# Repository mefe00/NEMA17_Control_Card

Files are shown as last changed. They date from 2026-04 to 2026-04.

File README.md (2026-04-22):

# STM32G tabanlı NEMA17 sürücü kartı 

> Bu proje, NEMA17 gibi step motorları alanın az olduğu yerlerde hem kompakt boyut sağlamak hemde kablo karmaşını en aza indirmek için tasarlanmıştır.

resim

## 📋 Özellikler

* MCU: STM32G431CBT6
* Çalışma Gerilimi: 24V
* Haberleşme: CAN/CAN-FD: Kartta iki tane CAN konnektörü vardır. Bu sayede aynı karta veya aynı CAN hattı üzerindeki başka bir kartla haberleşmek için bir konnektöre giriş yapıp diğer konnektörden çıkabilirsiniz ve diğer cihaza giriş yapabilirsiniz. Dikkat: Eğer kartı CAN                   hattının son cihazı ise 60 ohmları buna uygun bir şekilde montajlayın !!!!
              I2C: Eğer motorda redüktör varsa ve kartın arkasındaki encoder kullanılmak istenmezse harici ucuz bir encoder (AS5600) girişi redüktör ucundan alınması içindir. Diğer amacı ise yine bir encoder bağlayıp redüktör boşluğu (backlash) tespiti yapılabilmesi içindir.
              USART: Debug veya direkt haberleşme sağlanabilmesi için. 
* Koruma: 26V seviyesini aşarsa sürücü koruması için TVS diyot
* Encoder: AS5147-P ----> Kartın direkt arkasında bulunur ve pahalı ve kaliteli seçilmesinin sebebi ise redüktör eklenen motorlarda milin daha hızlı dönmesinden dolayı açı verisinin kaçmasını engellemek içindir.
           AS5600   ----> Karta harici bir şekilde girilebilir. Kart üzerinde bunun için harici I2C konnektörü vardır.
* NTC: Kart üzerindeki sıcaklığı tespit etmek için kullanılabilir.
* FAN: NTC'den alınan verilere göre veya manuel soğutma için 24V fan desteği vardır.
* Sürücü: TMC2209 seçilmiştir ama TMC2208 veya pinleri uyuşan başka bir sürücüde kullanılabilir. 

## 📂 Depo İçeriği

* `/Hardware`: KiCAD şematik (`.kicad_sch`) ve PCB (`.kicad_pcb`) tasarım dosyaları.
* `/production`: Üretime hazır Gerber ve Drill dosyaları.
* `/software`: Kartın robot kol eksenlerindeki motorları kontrolü için hazırlanmış gömülü kodu.

## Tavsiyeler

* Güç girişine 50V / 1000uF seviyelerinde bir elektrolit kapasitör eklenmesi.
* Sürücülerin bozulması durumları düşünüldüğü için modül olarak yerleştirilmiştir ve modulün altı boş olduğu için burayada 50V / 220uF seviyelerinde elektrolit kapasitör eklenmesi.
* Daha kararlı bir çalışma olabilmesi için sürücü üzerine soğutucu (heatsink) yerleştirin.
* Daha soğuk bir çalışma için soğutu bloğu buck converter üzerinede yerleştirebilirsiniz.

## Diğer Görseller

resim

resim

FAN

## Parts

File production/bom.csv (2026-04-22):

Designator | Footprint | Quantity | Value | LCSC Part # | Description
C1, C2 | 1206 | 2 | 2.2uF | C50254 | Ceramic Capacitor 2.2uF 50V X7R 10%
C10, C12, C15, C19, C20, C21, C26, C27 | 603 | 8 | 100nF | C14663
C13, C16, C9 | 603 | 3 | 10nF | C100042 | Soft-Start (SS/TR) kapasitörü.
C17, C18, C23, C25, C28 | 603 | 5 | 1uF | C15849
C22, C24 | 603 | 2 | 20pF | C1648
C3 | 603 | 1 | 0.1uF | C53084455 | C3 giriş filtresi, C8 ise BOOT kapasitörü
C4 | 603 | 1 | 6800pF | C107097 | Kompanzasyon (COMP) ağı kapasitörü.
C5 | 603 | 1 | 39pF | C107049 | Kompanzasyon (COMP) ağı yüksek frekans kapasitörü (NP0/C0G dielektrik).
C6, C7 | 805 | 2 | 47uF | C6119904 | 5V çıkış hattı filtre kapasitörleri. 5V için 10V voltaj dayanımı yeterlidir.
C8 | 603 | 1 | 10uF | C53084455
D1 | D_SMA | 1 | B260 | C109094 | 60V 2A Schottky Diyot. (MCU ve sensörler için 2A fazlasıyla yeterli)
D2 | D_SOD-323 | 1 | 1N5819WS | C191023
D3 | DIO_PESD2CAN_215 | 1 | PESD2CANFD24 | C5278878
D4 | 603 | 1 | GREEN | C2986048
D5 | 603 | 1 | RED | C183848
D6 | D_SMB | 1 | SMBJ26A-13-F | C135062 | TVS Diode Unidirectional 26V WM 600W
FB1 | 603 | 1 | FerriteBead | C14709
J1 | AMASS_XT30U-F_1x02_P5.0mm_Vertical | 1 | Conn_01x02_Socket
J10, J8, J9 | JST_GH_SM04B-GHS-TB_1x04-1MP_P1.25mm_Horizontal | 3 | Conn_01x04_Socket | C189895
J2, J3 | PinHeader_1x02_P2.54mm_Vertical | 2 | Conn_01x02_Pin
J4 | JST_PH_S4B-PH-K_1x04_P2.00mm_Horizontal | 1 | Conn_01x04_Socket
J5, J6 | JST_GH_SM02B-GHS-TB_1x02-1MP_P1.25mm_Horizontal | 2 | Conn_01x02_Socket | C189893
L1 | L_6.3x6.3_H3 | 1 | 8.2uH | C167222 | 6x6x2.8mm SMD Bobin (Sunlord). Doyuma ulaşma akımı 2.5A, bu sistem için ideal.
Q1 | SOT-23 | 1 | AO3400A | C20917
R1 | 603 | 1 | 162k | C2998114 | EN (Enable) pini voltaj bölücü alt direnci.
R11 | 603 | 1 | 2.2k -1k | C22548
R12, R15, R18, R8, R9 | 603 | 5 | 10k | C98220
R13 | 603 | 1 | 330R | C105881
R16, R17 | 603 | 2 | 60R | C85834
R2 | 603 | 1 | 523k | C5126197 | EN (Enable) pini voltaj bölücü üst direnci.
R3 | 603 | 1 | 84.5k | C855976 | RT/CLK frekans ayar direnci.
R4 | 603 | 1 | 13k | C137796 | Kompanzasyon (COMP) ağı direnci.
R5 | 603 | 1 | 53.6k | C2930115 | Feedback (FB) üst direnci (Hassas 5V çıkış için %1 tolerans).
R6 | 603 | 1 | 10.2k | C22772 | Feedback (FB) alt direnci (Hassas 5V çıkış için %1 tolerans).
R7 | 603 | 1 | 100R | C105588
SW1 | SW_Push_1P1T_NO_CK_KMR2 | 1 | SW_Push | C99271
U1 | LQFP-48_7x7mm_P0.5mm | 1 | STM32G431CBT6 | C529355 | MCU
U2 | SOT-23-5 | 1 | AP2112K-3.3 | C51118 | 3.3V LDO
U3 | TI_SO-PowerPAD-8_ThermalVias | 1 | TPS54360DDA | C465733 | 60V, 3.5A Step-Down Converter
U4 | SOIC-8_3.9x4.9mm_P1.27mm | 1 | MCP2562-E-SN | C53609 | CAN entegresi
U5 | MODULE_TMC2209_SILENTSTEPSTICK | 1 | TMC2209_SILENTSTEPSTICK
U6 | TSSOP-14_AMS | 1 | AS5147P-HTSM | C22426928 | Encoder
Y1 | Crystal_SMD_3225-4Pin_3.2x2.5mm | 1 | Crystal_GND24_Small | C7275084 | Kristal

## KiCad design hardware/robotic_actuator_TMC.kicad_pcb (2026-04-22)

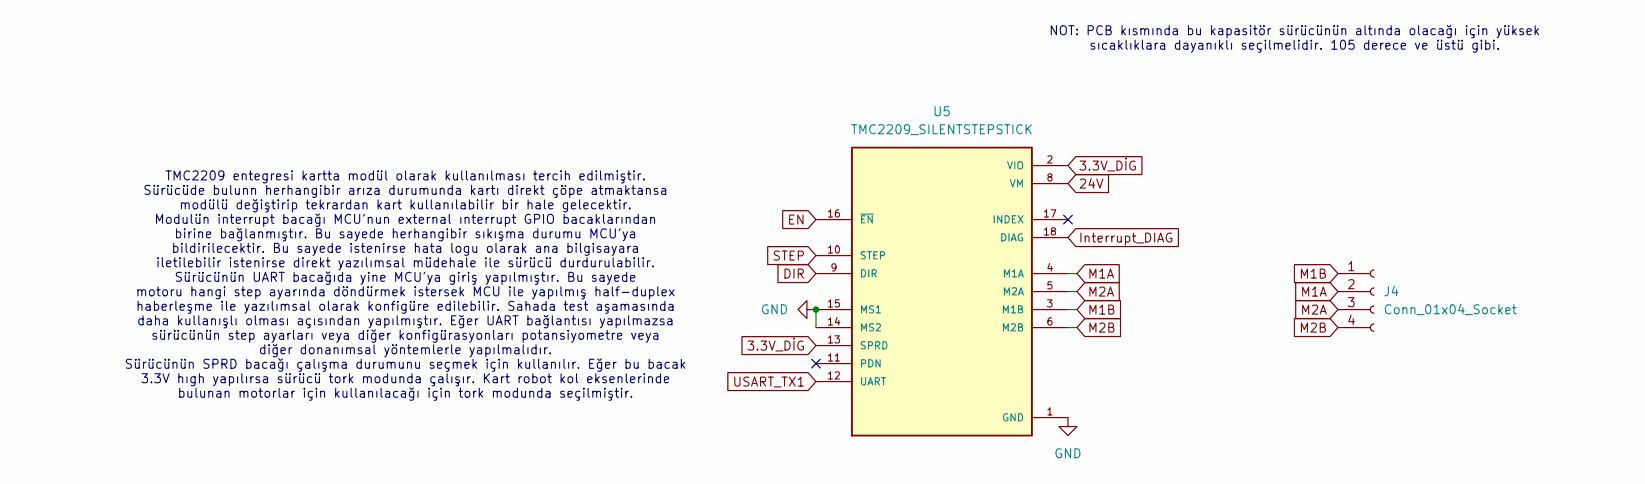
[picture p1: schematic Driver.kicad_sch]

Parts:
J4: Conn_01x04_Socket; JST_PH_S4B-PH-K_1x04_P2.00mm_Horizontal
U5: TMC2209_SILENTSTEPSTICK; MODULE_TMC2209_SILENTSTEPSTICK; PARTREV 1.20

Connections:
3.3V_DİG: U5.2 (VIO), U5.13 (SPRD); also elsewhere on the board
24V: U5.8 (VM); also elsewhere on the board
DIR: U5.9 (DIR); also elsewhere on the board
EN: U5.16 (~EN); also elsewhere on the board
GND: U5.1 (GND), U5.7 (GND), U5.14 (MS2), U5.15 (MS1); also elsewhere on the board
Interrupt_DIAG: U5.18 (DIAG); also elsewhere on the board
M1A: J4.2, U5.4 (M1A)
M1B: J4.1, U5.3 (M1B)
M2A: J4.3, U5.5 (M2A)
M2B: J4.4, U5.6 (M2B)
STEP: U5.10 (STEP); also elsewhere on the board
USART_TX1: U5.12 (UART); also elsewhere on the board

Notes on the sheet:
TMC2209 entegresi kartta modül olarak kullanılması tercih edilmiştir. Sürücüde bulunn herhangibir arıza durumunda kartı direkt çöpe atmaktansa modülü değiştirip tekrardan kart kullanılabilir bir hale gelecektir. Modulün interrupt bacağı MCU'nun external ınterrupt GPIO bacaklarından birine bağlanmış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
NOT: PCB kısmında bu kapasitör sürücünün altında olacağı için yüksek sıcaklıklara dayanıklı seçilmelidir. 105 derece ve üstü gibi.

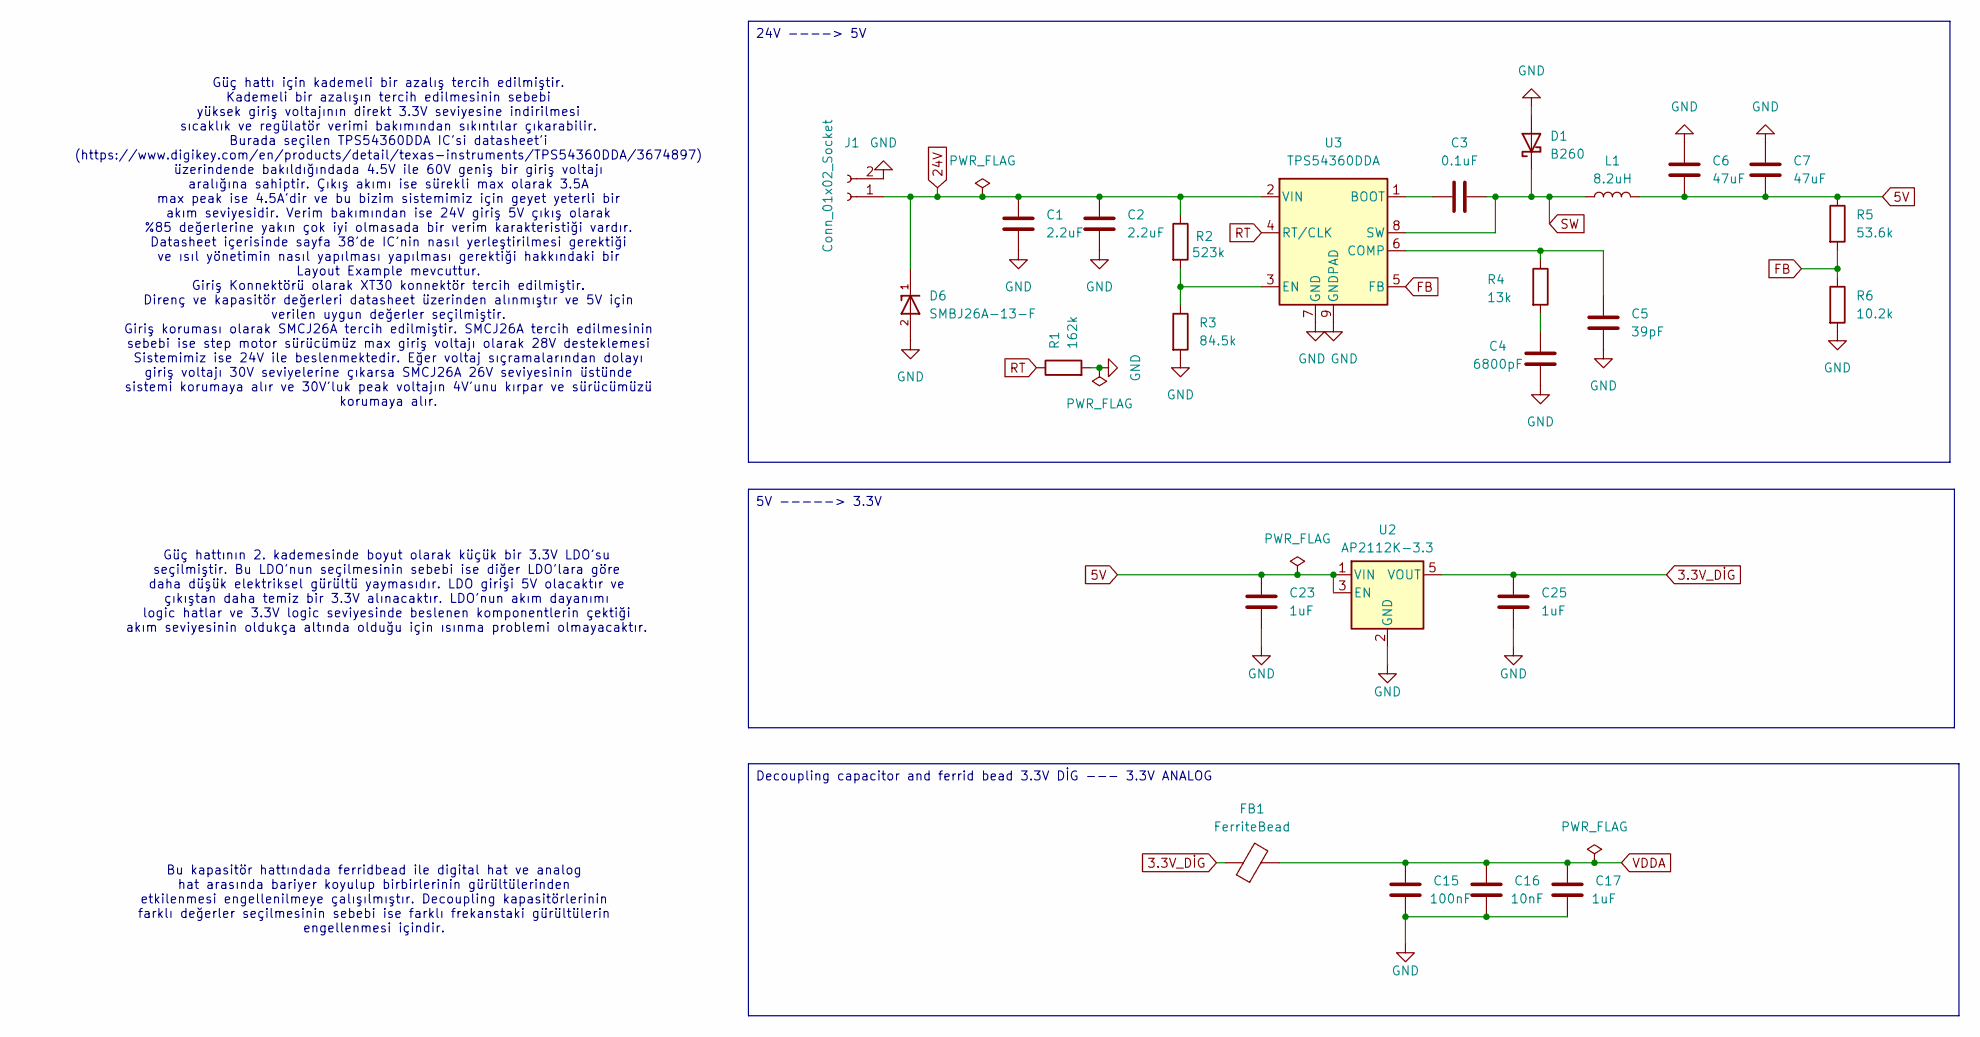
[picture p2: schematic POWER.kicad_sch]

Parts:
C1, C2: 2.2uF; C_1206_3216Metric
C3: 0.1uF; C_0603_1608Metric
C4: 6800pF; C_0603_1608Metric
C5: 39pF; C_0603_1608Metric
C6, C7: 47uF; C_0805_2012Metric
C15: 100nF; C_0603_1608Metric
C16: 10nF; C_0603_1608Metric
C17, C23, C25: 1uF; C_0603_1608Metric
D1: B260; D_SMA
D6: SMBJ26A-13-F; D_SMB; PARTREV 20 - 2
FB1: FerriteBead; L_0603_1608Metric
J1: Conn_01x02_Socket; AMASS_XT30U-F_1x02_P5.0mm_Vertical
L1: 8.2uH; L_6.3x6.3_H3
R1: 162k; R_0603_1608Metric
R2: 523k; R_0603_1608Metric
R3: 84.5k; R_0603_1608Metric
R4: 13k; R_0603_1608Metric
R5: 53.6k; R_0603_1608Metric
R6: 10.2k; R_0603_1608Metric
U2: AP2112K-3.3; SOT-23-5
U3: TPS54360DDA; TI_SO-PowerPAD-8_ThermalVias

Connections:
3.3V_DİG: C25.1, FB1.1, U2.5 (VOUT); also elsewhere on the board
5V: C6.1, C7.1, C23.1, L1.2, R5.1, U2.1 (VIN), U2.3 (EN); also elsewhere on the board
24V: C1.1, C2.1, D6.1, J1.1, R2.1, U3.2 (VIN); also elsewhere on the board
FB: R5.2, R6.1, U3.5 (FB)
GND: C1.2, C2.2, C4.1, C5.1, C6.2, C7.2, C15.2, C16.2, C17.2, C23.2, C25.2, D1.2 (A), D6.2, J1.2, R1.2, R3.2, R6.2, U2.2 (GND), U3.7 (GND), U3.9 (GNDPAD); also elsewhere on the board
unnamed: C4.2, R4.2
unnamed: C3.1, U3.1 (BOOT)
unnamed: C5.2, R4.1, U3.6 (COMP)
unnamed: R2.2, R3.1, U3.3 (EN)
RT: R1.1, U3.4 (RT/CLK)
SW: C3.2, D1.1 (K), L1.1, U3.8 (SW)
VDDA: C15.1, C16.1, C17.1, FB1.2; also elsewhere on the board

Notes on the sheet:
Güç hattının 2. kademesinde boyut olarak küçük bir 3.3V LDO'su seçilmiştir. Bu LDO'nun seçilmesinin sebebi ise diğer LDO'lara göre daha düşük elektriksel gürültü yaymasıdır. LDO girişi 5V olacaktır ve çıkıştan daha temiz bir 3.3V alınacaktır. LDO'nun akım dayanımı logic hatlar ve 3.3V logic seviyes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
Bu kapasitör hattındada ferridbead ile digital hat ve analog hat arasında bariyer koyulup birbirlerinin gürültülerinden etkilenmesi engellenilmeye çalışılmıştır. Decoupling kapasitörlerinin farklı değerler seçilmesinin sebebi ise farklı frekanstaki gürültülerin engellenmesi içindir.
Güç hattı için kademeli bir azalış tercih edilmiştir. Kademeli bir azalışın tercih edilmesinin sebebi yüksek giriş voltajının direkt 3.3V seviyesine indirilmesi sıcaklık ve regülatör verimi bakımından sıkıntılar çıkarabilir. Burada seçilen TPS54360DDA IC'si datasheet'i (https://www.digikey.com/en/p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
Decoupling capacitor and ferrid bead 3.3V DİG --- 3.3V ANALOG
5V -----> 3.3V
24V ----> 5V

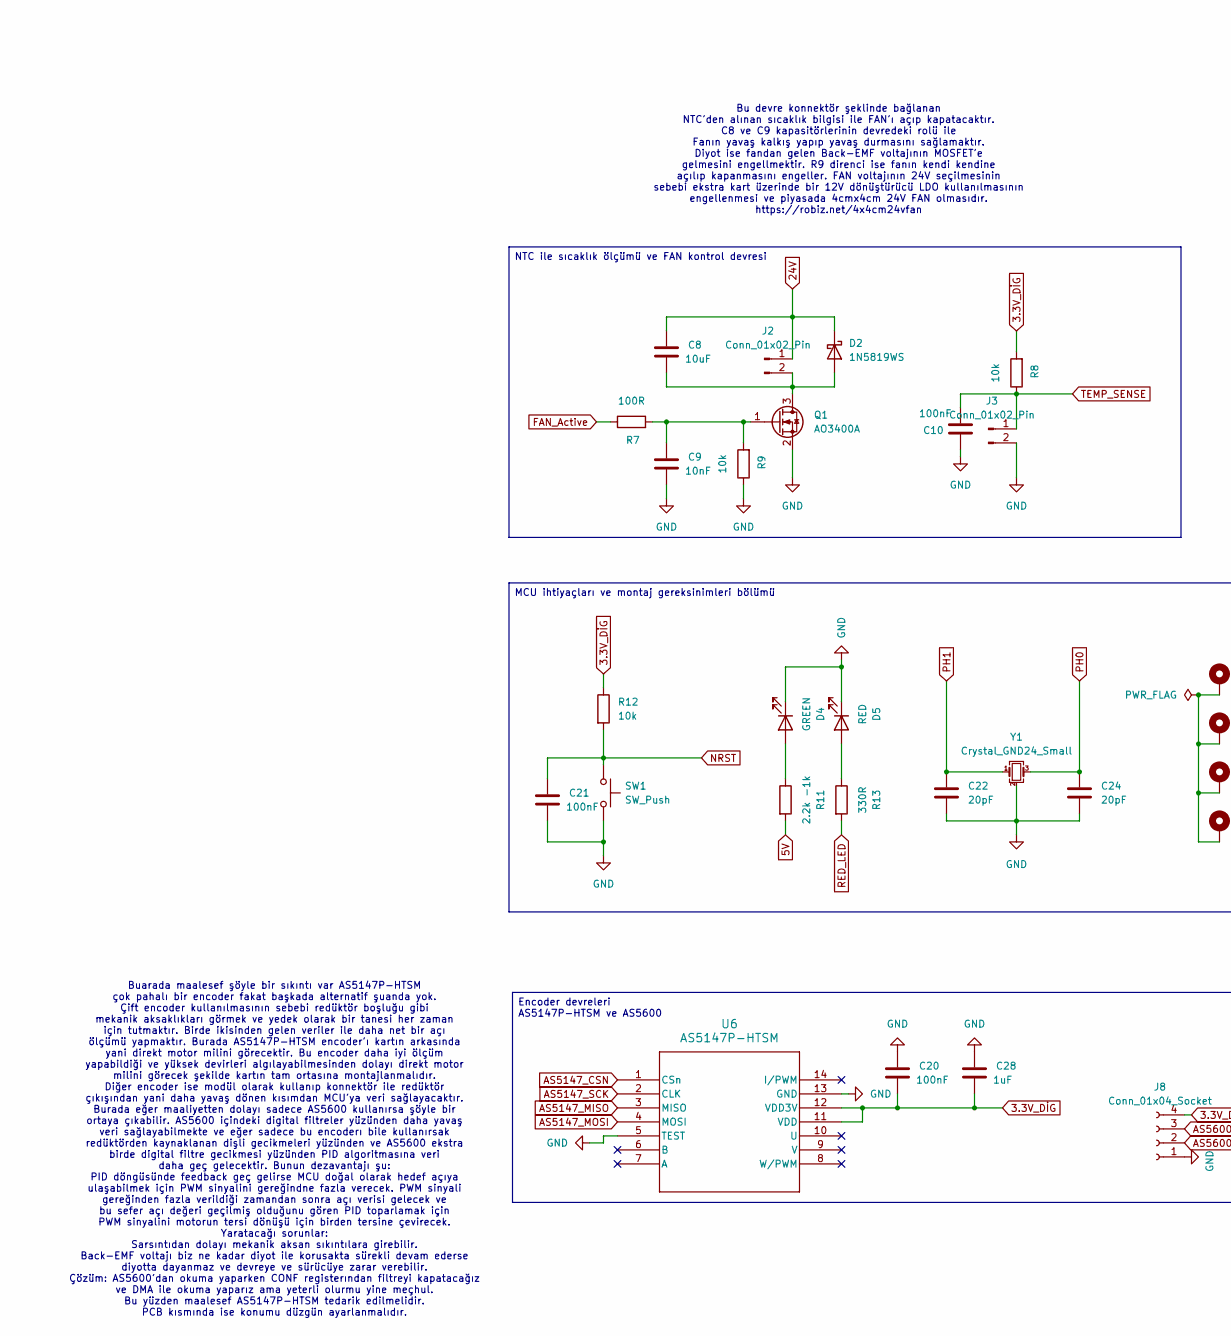
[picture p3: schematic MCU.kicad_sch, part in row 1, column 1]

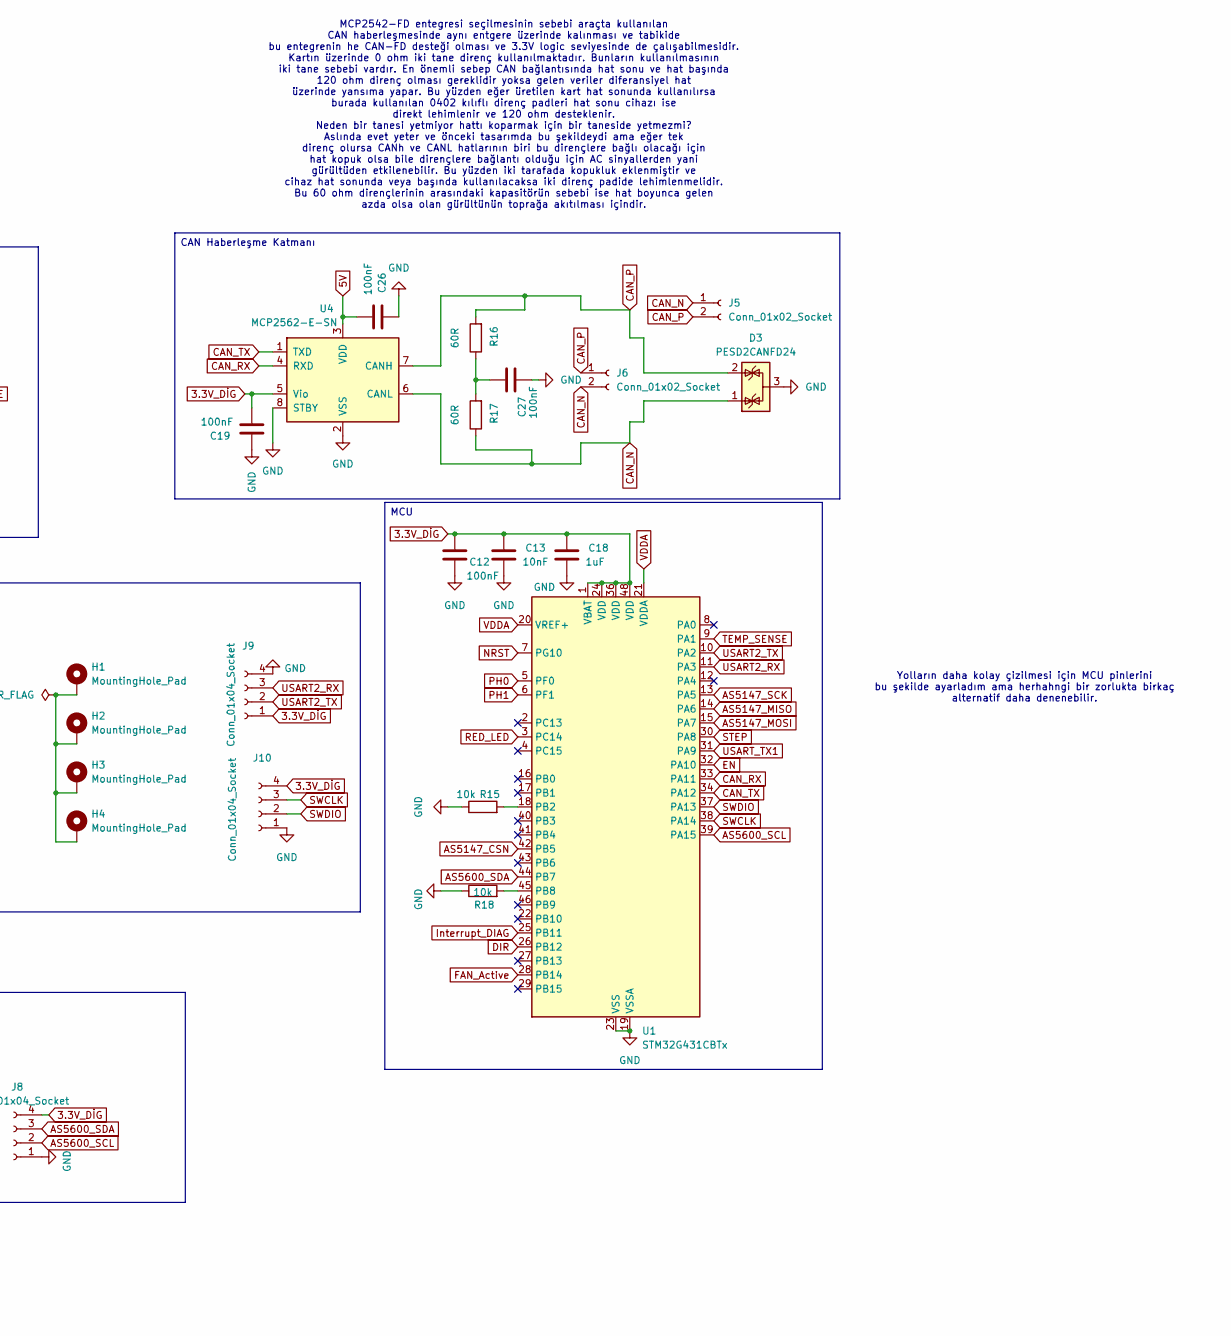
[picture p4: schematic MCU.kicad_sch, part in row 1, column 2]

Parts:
C8: 10uF; C_0603_1608Metric
C9, C13: 10nF; C_0603_1608Metric
C10, C12, C19, C20, C21, C26, C27: 100nF; C_0603_1608Metric
C18, C28: 1uF; C_0603_1608Metric
C22, C24: 20pF; C_0603_1608Metric
D2: 1N5819WS; D_SOD-323
D3: PESD2CANFD24; DIO_PESD2CAN_215
D4: GREEN; LED_0603_1608Metric
D5: RED; LED_0603_1608Metric
H1, H2, H3, H4: MountingHole_Pad; MountingHole_3.5mm
J2, J3: Conn_01x02_Pin; PinHeader_1x02_P2.54mm_Vertical
J5, J6: Conn_01x02_Socket; JST_GH_SM02B-GHS-TB_1x02-1MP_P1.25mm_Horizontal
J8, J9, J10: Conn_01x04_Socket; JST_GH_SM04B-GHS-TB_1x04-1MP_P1.25mm_Horizontal
Q1: AO3400A; SOT-23
R7: 100R; R_0603_1608Metric
R8, R9, R12, R15, R18: 10k; R_0603_1608Metric
R11: 2.2k -1k; R_0603_1608Metric
R13: 330R; R_0603_1608Metric
R16, R17: 60R; R_0603_1608Metric
SW1: SW_Push; SW_Push_1P1T_NO_CK_KMR2
U1: STM32G431CBTx; LQFP-48_7x7mm_P0.5mm
U4: MCP2562-E-SN; SOIC-8_3.9x4.9mm_P1.27mm
U6: AS5147P-HTSM; TSSOP-14_AMS
Y1: Crystal_GND24_Small; Crystal_SMD_3225-4Pin_3.2x2.5mm

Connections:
3.3V_DİG: C12.1, C13.1, C18.1, C19.2, C20.2, C28.2, J8.4, J9.1, J10.4, R8.2, R12.1, U1.1 (VBAT), U1.24 (VDD), U1.36 (VDD), U1.48 (VDD), U4.5 (Vio), U6.11 (VDD), U6.12 (VDD3V); also elsewhere on the board
5V: C26.2, R11.2, U4.3 (VDD); also elsewhere on the board
24V: C8.1, D2.1 (K), J2.1; also elsewhere on the board
AS5147_CSN: U1.42 (PB5), U6.1 (CSn)
AS5147_MISO: U1.14 (PA6), U6.3 (MISO)
AS5147_MOSI: U1.15 (PA7), U6.4 (MOSI)
AS5147_SCK: U1.13 (PA5), U6.2 (CLK)
AS5600_SCL: J8.2, U1.39 (PA15)
AS5600_SDA: J8.3, U1.44 (PB7)
CAN_N: D3.1 (K), J5.1, J6.2, R17.1, U4.6 (CANL)
CAN_P: D3.2 (K), J5.2, J6.1, R16.2, U4.7 (CANH)
CAN_RX: U1.33 (PA11), U4.4 (RXD)
CAN_TX: U1.34 (PA12), U4.1 (TXD)
DIR: U1.26 (PB12); also elsewhere on the board
EN: U1.32 (PA10); also elsewhere on the board
FAN_Active: R7.1, U1.28 (PB14)
GND: C9.2, C10.2, C12.2, C13.2, C18.2, C19.1, C20.1, C21.2, C22.2, C24.2, C26.1, C27.2, C28.1, D3.3 (A), D4.1 (K), D5.1 (K), J3.2, J8.1, J9.4, J10.1, Q1.2 (S), R9.1, R15.1, R18.1, SW1.2, U1.19 (VSSA), U1.23 (VSS), U1.35 (VSS), U1.47 (VSS), U4.2 (VSS), U4.8 (STBY), U6.5 (TEST), U6.13 (GND), Y1.2 (G), Y1.4 (G); also elsewhere on the board
Interrupt_DIAG: U1.25 (PB11); also elsewhere on the board
NRST: C21.1, R12.2, SW1.1, U1.7 (PG10)
unnamed: C27.1, R16.1, R17.2
unnamed: C8.2, D2.2 (A), J2.2, Q1.3 (D)
unnamed: D4.2 (A), R11.1
unnamed: D5.2 (A), R13.1
unnamed: C9.1, Q1.1 (G), R7.2, R9.2
unnamed: R15.2, U1.18 (PB2)
unnamed: R18.2, U1.45 (PB8)
PH0: C24.1, U1.5 (PF0), Y1.3
PH1: C22.1, U1.6 (PF1), Y1.1
RED_LED: R13.2, U1.3 (PC14)
STEP: U1.30 (PA8); also elsewhere on the board
SWCLK: J10.3, U1.38 (PA14)
SWDIO: J10.2, U1.37 (PA13)
TEMP_SENSE: C10.1, J3.1, R8.1, U1.9 (PA1)
USART2_RX: J9.3, U1.11 (PA3)
USART2_TX: J9.2, U1.10 (PA2)
USART_TX1: U1.31 (PA9); also elsewhere on the board
VDDA: U1.20 (VREF+), U1.21 (VDDA); also elsewhere on the board

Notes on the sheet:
Buarada maalesef şöyle bir sıkıntı var AS5147P-HTSM çok pahalı bir encoder fakat başkada alternatif şuanda yok. Çift encoder kullanılmasının sebebi redüktör boşluğu gibi mekanik aksaklıkları görmek ve yedek olarak bir tanesi her zaman için tutmaktır. Birde ikisinden gelen veriler ile daha net bir a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
Bu devre konnektör şeklinde bağlanan NTC'den alınan sıcaklık bilgisi ile FAN'ı açıp kapatacaktır. C8 ve C9 kapasitörlerinin devredeki rolü ile Fanın yavaş kalkış yapıp yavaş durmasını sağlamaktır. Diyot ise fandan gelen Back-EMF voltajının MOSFET'e gelmesini engellmektir. R9 direnci ise fanın kendi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
MCP2542-FD entegresi seçilmesinin sebebi araçta kullanılan CAN haberleşmesinde aynı entgere üzerinde kalınması ve tabikide bu entegrenin he CAN-FD desteği olması ve 3.3V logic seviyesinde de çalışabilmesidir. Kartın üzerinde 0 ohm iki tane direnç kullanılmaktadır. Bunların kullanılmasının iki tane 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
Yolların daha kolay çizilmesi için MCU pinlerini bu şekilde ayarladım ama herhahngi bir zorlukta birkaç alternatif daha denenebilir.
MCU
MCU ihtiyaçları ve montaj gereksinimleri bölümü
CAN Haberleşme Katmanı
NTC ile sıcaklık ölçümü ve FAN kontrol devresi
Encoder devreleri AS5147P-HTSM ve AS5600

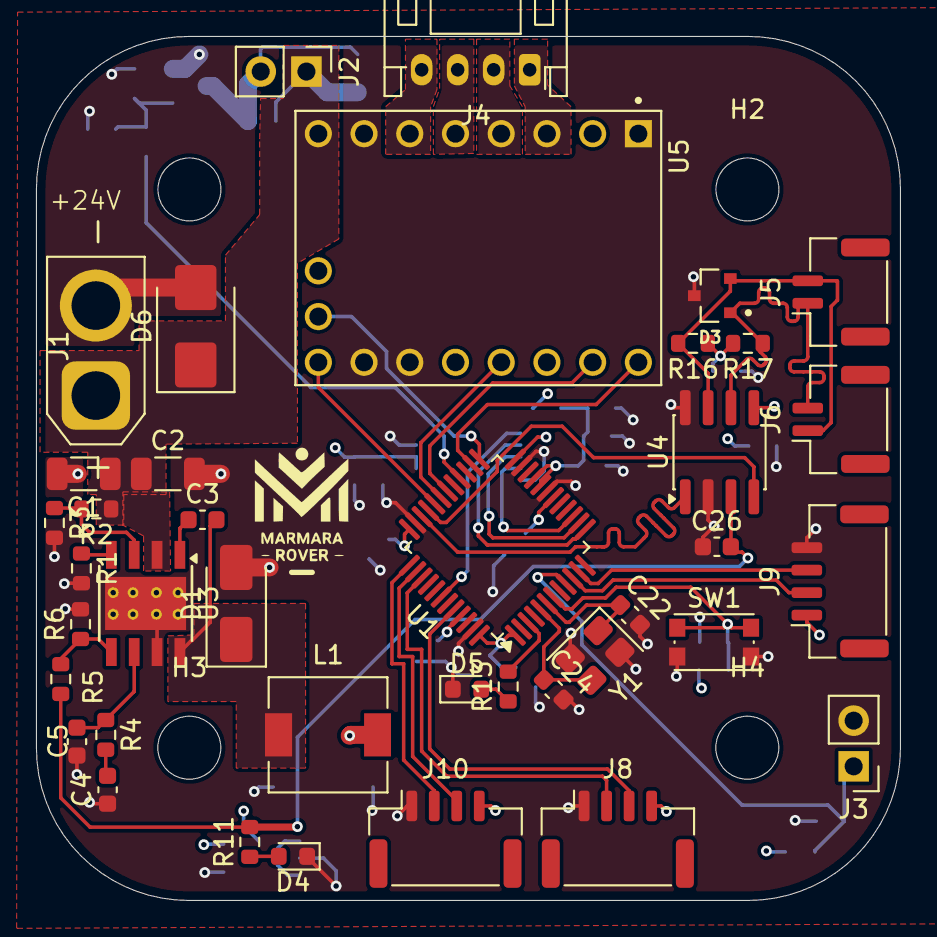
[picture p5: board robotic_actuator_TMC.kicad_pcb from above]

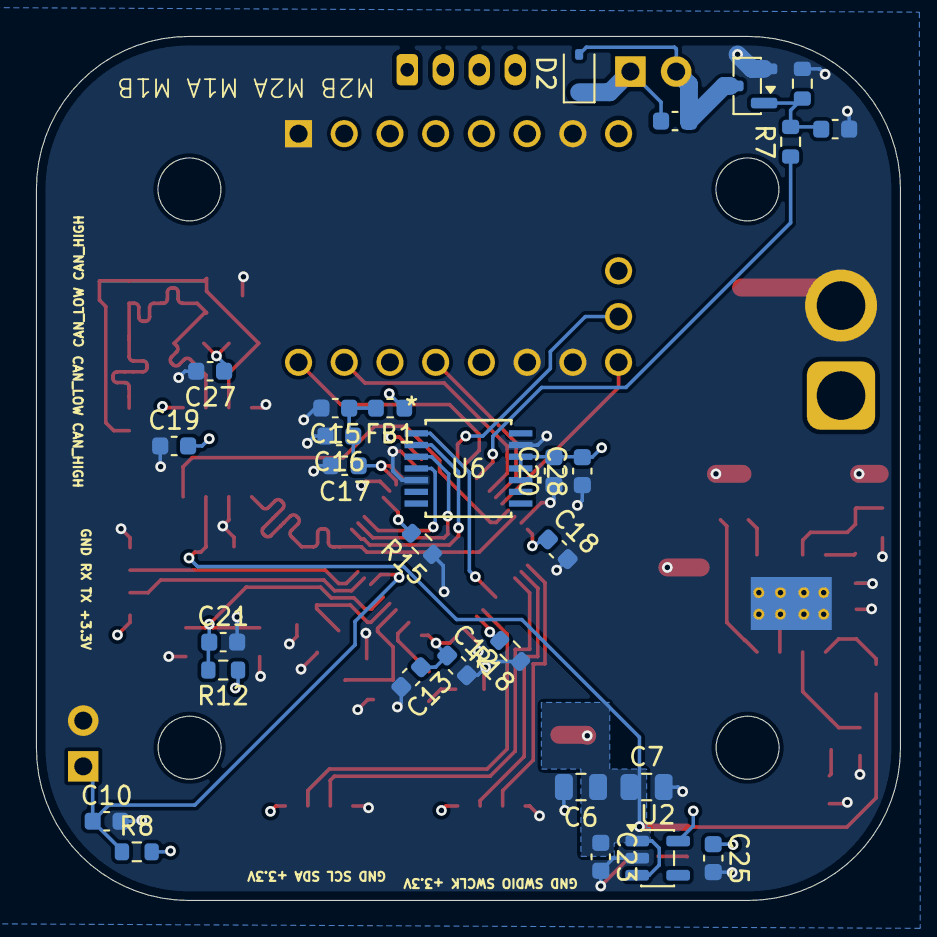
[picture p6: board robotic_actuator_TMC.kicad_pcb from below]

Board: 4 copper layers, 48.0 x 48.0 mm, 73 parts (29 on the bottom side), 48 nets.

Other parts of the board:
-: LOGO; Logo
